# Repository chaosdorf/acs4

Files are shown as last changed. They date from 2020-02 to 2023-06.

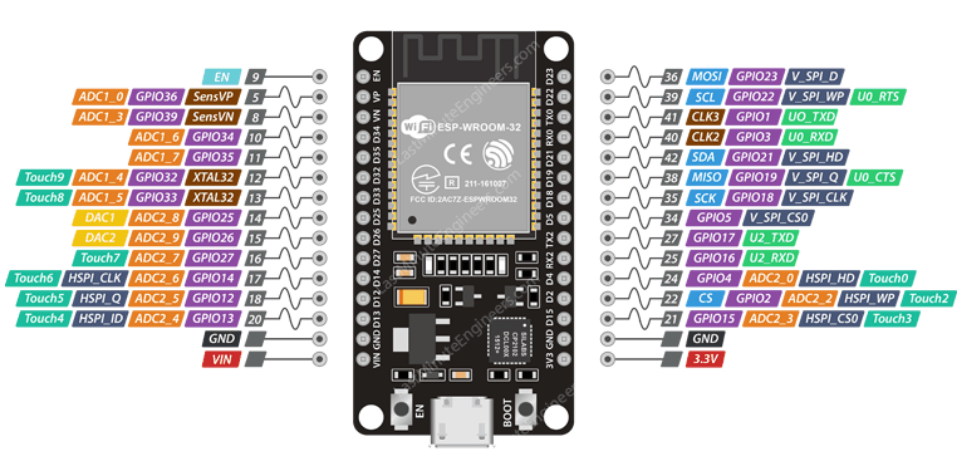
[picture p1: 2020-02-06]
pcb/prototyp/slave/ESP32_Pinout.png

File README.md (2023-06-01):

# Access control system 4 

Die (geplante) Türsteuerung für die Türen im neuen Dorf auf der Sonnenstraße.

## Benutzung

Gäste können die Klingel betätigen, dann klingelt es.

Mitglieder können mit ihrem iButton oder SSH-Key die Tür temporär öffnen.

(public schalten wie im alten Dorf ist in diesem Haus wohl leider unpraktikabel.)

Einzelne Menschen sind in der Lage, Schlüssel zu registrieren und zu revoken.

## Hardware

Fürs Erste haben wir eine Minimallösung vor mit nur einer Platine mit einem ESP32-C3:

- speichert die iButton-IDs
- steuert die Aktoren an 12V Output
- Unlock über WiFi (SSH-Emulation)
- Update der IDs über Git
- gute Rust-Unterstützung

<details>
<summary>Die vollständige Lösung sollte auf zwei Platinen aufgeteilt sein:</summary>

[Blockschaltbild](src/Blockbild_Uebersicht_rev04.pdf)

### Server-Board
- Steuert die Aktoren an 12V Output
- Speichert die iButton IDs auf einer SD
- Ethernet nutzt ein Olimex Board ESP32 rev E
- Stromausfall erkennung

[Olimex Shop](https://www.olimex.com/Products/IoT/ESP32/ESP32-GATEWAY/open-source-hardware)

[Github Projekt Olimex](https://github.com/OLIMEX/ESP32-GATEWAY/tree/master/HARDWARE)

[ESP32 Gateway Schematic rev E](src/ESP32-GATEWAY_Rev_E_color.pdf)

### Client-Board
- iButton Reader
- LED Output
- Klingel Taster input 1
- Klingel Taster input 2
- Display output für eInk
- WS2812 LED Output

(jeweils für Außen- und Innentür)

[Waveshare eInk - Shop](https://eckstein-shop.de/Waveshare-27-inch-264x176-E-Ink-E-Paper-Raw-Display-three-color-Arduino)

</detail>

### Elektrisches Schloss
Unsere Tür hat drei Modi:
 * zu (Panikfunktion)
 * Summer
 * offen

Wir hatten überlegt, einen Motor an den Schlosszylinder anzuschließen, um zwischen diesen drei Modi umschalten zu können.
(Bei unserem Versuch mit einem Abus-Motor stand dann allerdings die Tür offen, weil sich der Motor unbedingt neu kalibrieren musste.)

Deswegen ist es wohl am einfachsten, die Tür einfach in dem Summer-Zustand zu lassen.

## Software

### Schlüsselspeicherung

Die Schlüssel liegen als Dateien in einem Git-Repo vor:

Es gibt beliebig viele `username-description.key`-Dateien,
die jeweils eine Zeile mit einer iButton-ID bzw. einem SSH-Key enthalten, z.B.:

```
ssh-ed22519 AAAAAAAAAAAAAAAAAAAAAAAAAAAAAAAA
```

```
iButton 1234567890
```

Sie ist ist signiert (minisign) von der ausstellenden Person und verschlüsselt (age) mit
 * einem gemeinsamen Public-Key
 * allen Public-Keys der Menschen aus dem Schlüssel-Team (diese sind auch im Repo hinterlegt)

Irgendwo läuft eine Software, die sich diese Änderungen zieht,
die die Dateien entschlüsselt und verifiziert und dann einen großen Blob erzeugt
und den verschlüsselt (mit libhydrogen).
Der ESP zieht sich davon regelmäßig die neueste Version.

Bis diese Software existiert, wird die große Schlüsselliste manuell geführt.

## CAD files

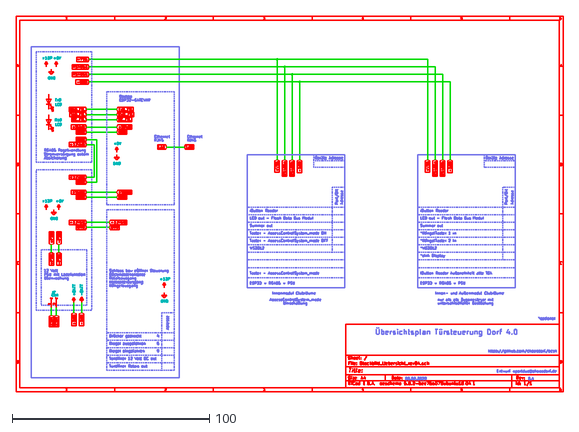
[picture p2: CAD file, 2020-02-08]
src/blockschaltbild/images/Blockbild_Uebersicht_rev04.dxf
277.0 x 190.0

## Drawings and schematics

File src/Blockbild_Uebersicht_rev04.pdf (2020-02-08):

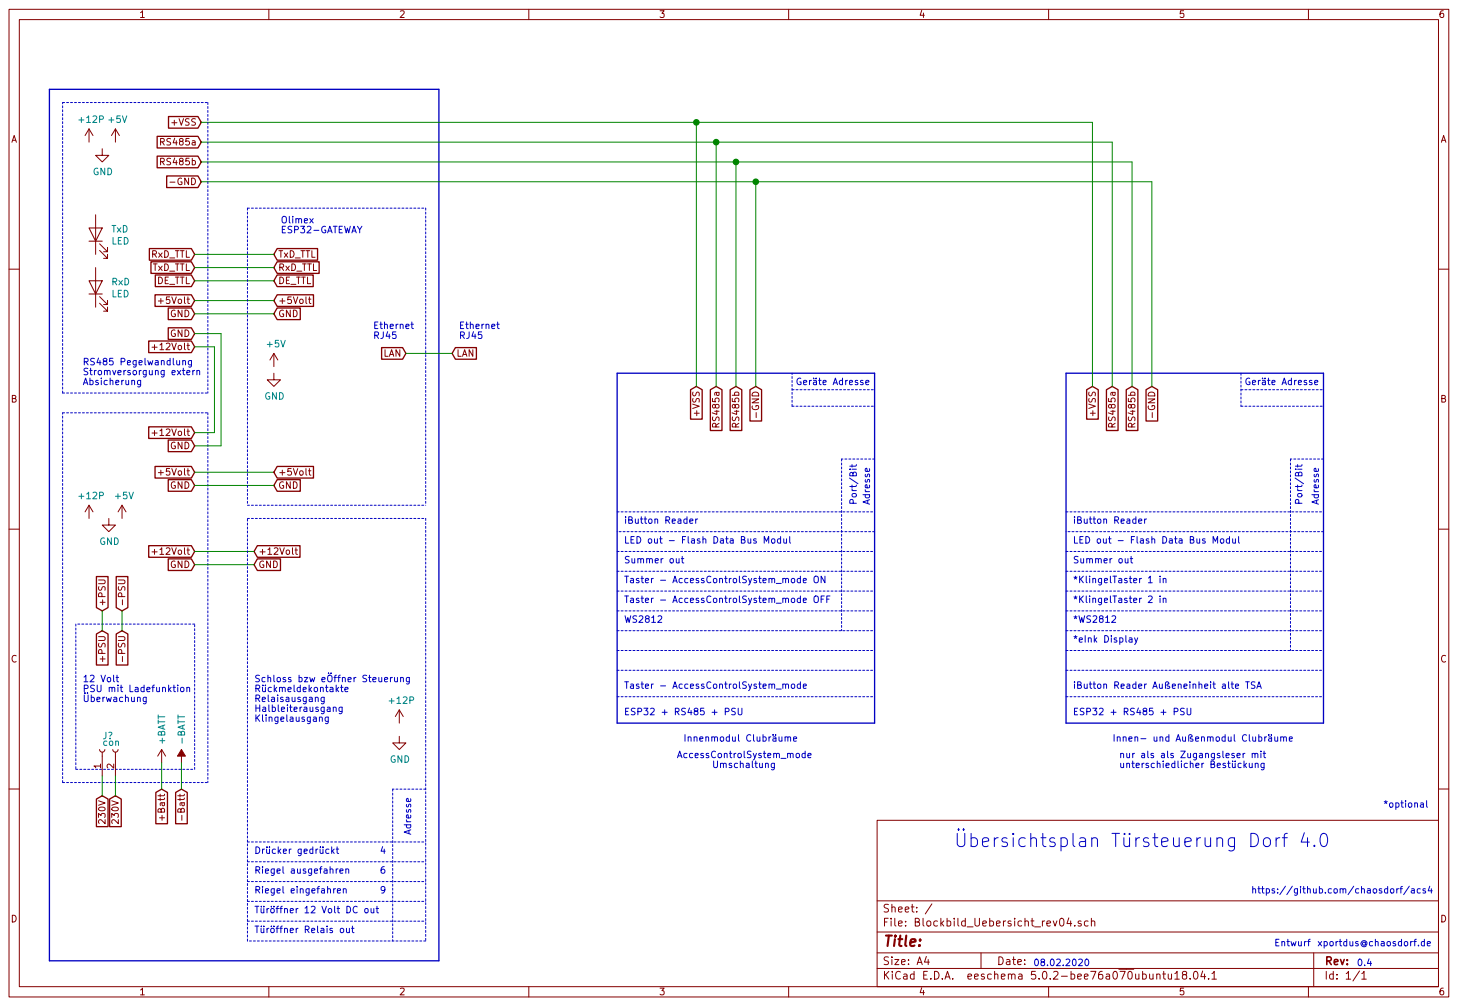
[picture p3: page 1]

iButton Reader *KlingelTaster 2 in

LED out - Flash Data Bus Modul Taster - AccessControlSystem_mode OFF

Taster - AccessControlSystem_mode ON WS2812

Schloss bzw eÖffner Steuerung Rückmeldekontakte Relaisausgang

iButton Reader Außeneinheit alte TSA

Innen- und Außenmodul Clubräume nur als als Zugangsleser mit

Türöffner Relais out Türöffner 12 Volt DC out Riegel ausgefahren Riegel eingefahren

Entwurf https://github.com/chaosdorf/acs4

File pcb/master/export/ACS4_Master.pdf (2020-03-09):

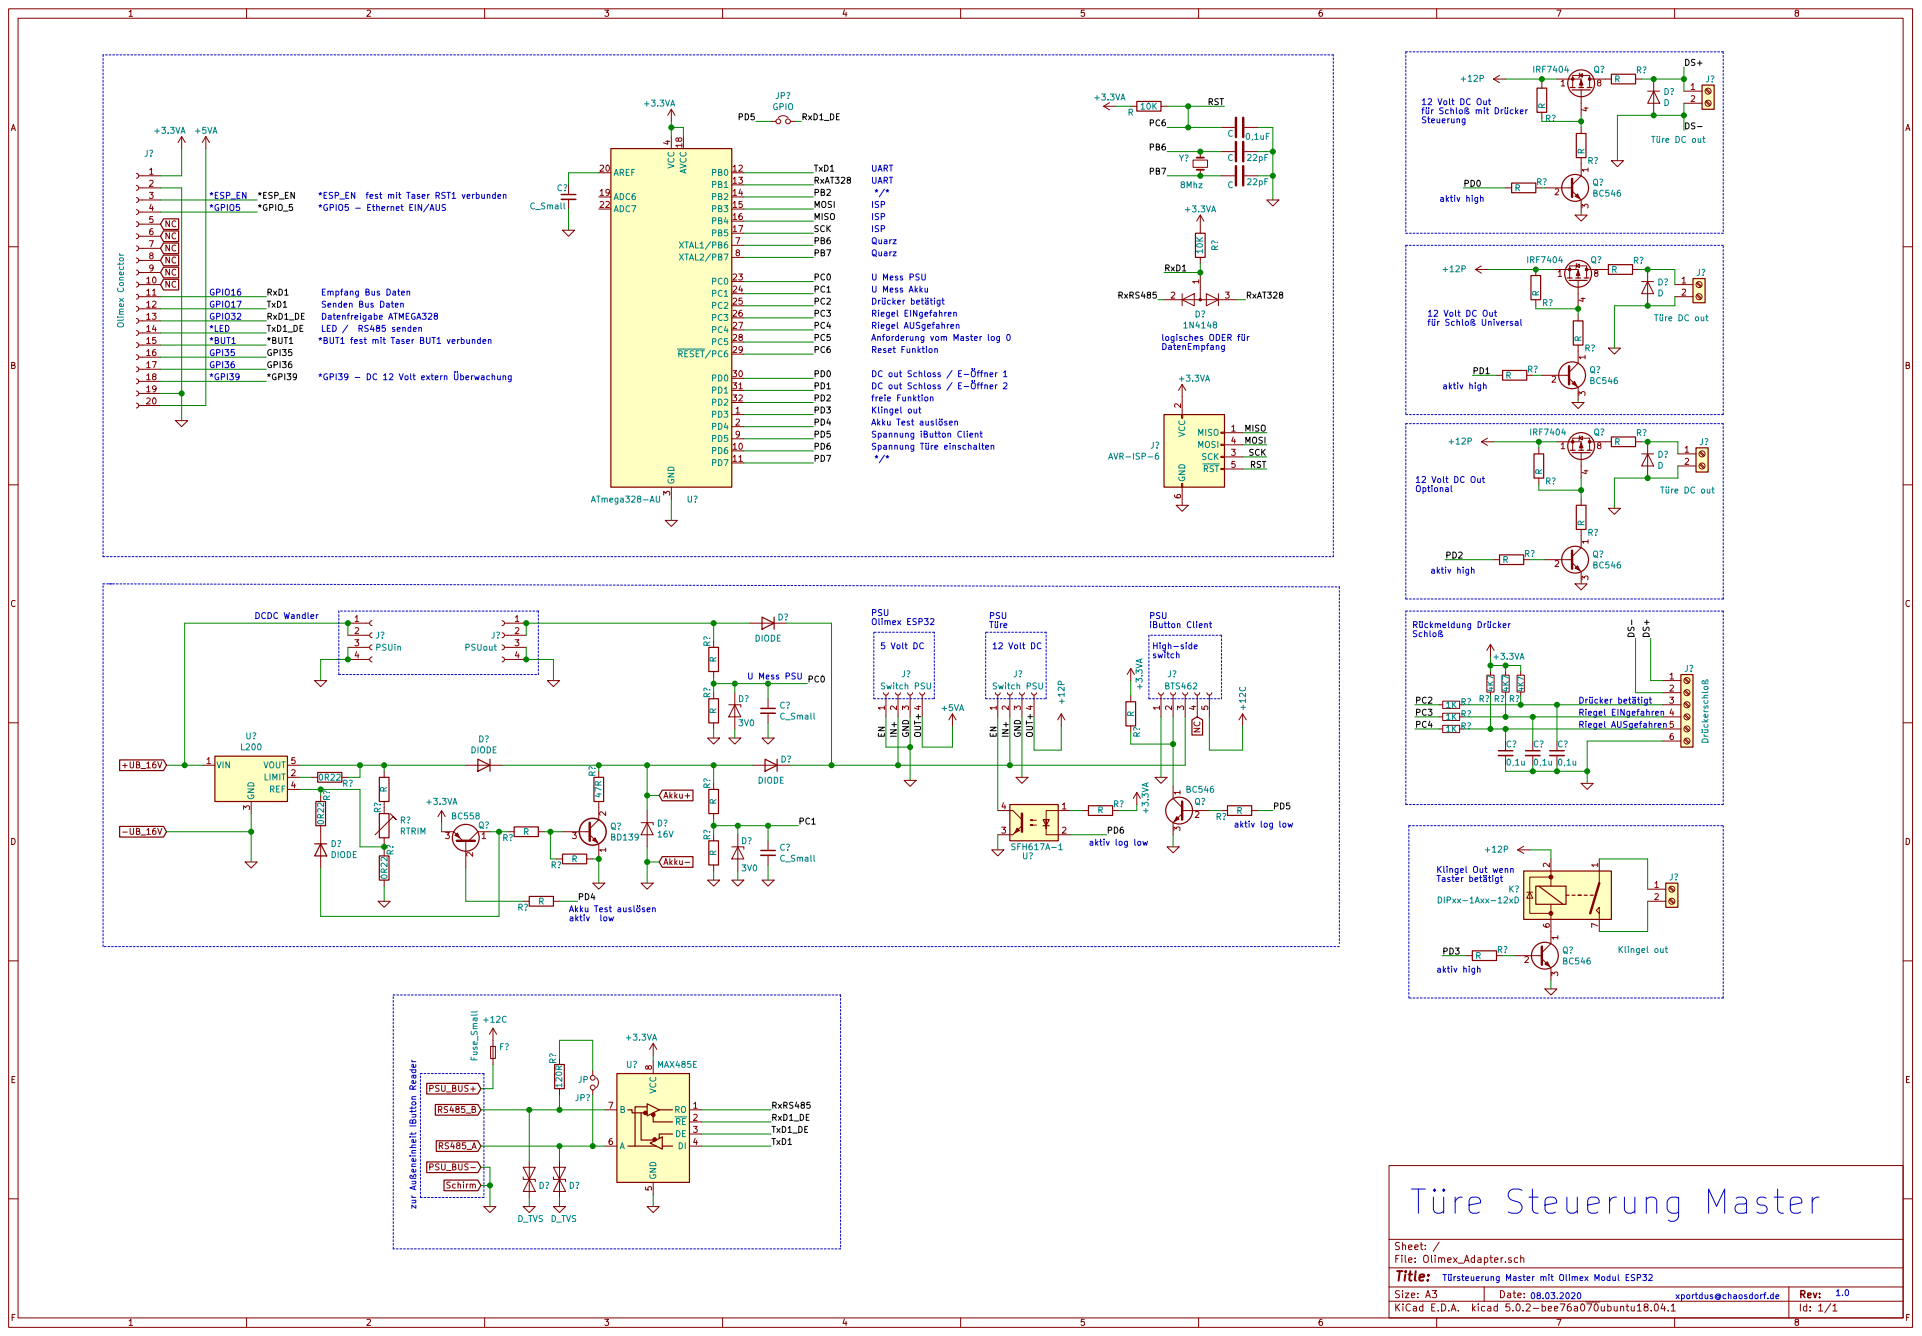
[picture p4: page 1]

U Mess PSU Quarz Quarz Spannung Türe einschalten Reset Funktion Drücker betätigt

12 Volt DC Out
für Schloß mit Drücker Steuerung

Riegel EINgefahren
Riegel AUSgefahren
Anforderung vom Master log 0

für Schloß Universal 12 Volt DC Out Optional R? R

DC out Schloss / E-Öffner 1
DC out Schloss / E-Öffner 2

*GPI39 - DC 12 Volt extern Überwachung

2 SCK 3 MOSI 4 RST 5 GND

Riegel EINgefahren 4

Akku Test auslösen aktiv low

File: Olimex_Adapter.sch Sheet: / Türe Steuerung Master

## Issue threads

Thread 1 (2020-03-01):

Schlüsselliste auf das Gerät bekommen

YtvwlD, 2020-03-01:
## allgemeine Beschreibung

Wir wollen ja iButtons nutzen, um die Türen zu öffnen. Dazu muss auf allen Geräten eine Liste vorhanden sein, welche iButtons berechtigt sind, die Türen zu öffnen. Dabei gibt es grob vier Anforderungen:

 * Schlüssel müssen zentral hinzugefügt werden können (z.B. Ausgabe an Neumitglieder)
 * Schlüssel müssen zentral entfernt werden können (z.B. Verlust eines Schlüssels)
 * die Liste von Schlüsseln darf nicht von Unbefugten gelesen werden (sowohl bei der Übertragung, als auf dem Speicher des Geräts); ansonsten können Schlüssel geklont werden
 * die Liste von Schlüsseln darf nicht von Unbefugten verändert werden (sowohl bei der Übertragung, als auf dem Speicher des Geräts); ansonsten können Schlüssel hinzugefügt werden

Das sind also zwei Ebenen: die Verteilung und die Integrität / Vertraulichkeit.

## Ansätze für Verteilung

### HTTPS

 * kann mit Client-Zertifikaten oder Auth-Headern auch direkt Integrität und Vertraulichkeit sicherstellen
 * Polling nötig
 * eigener Server nötig

###  mqtt

 * PubSub
 * bietet Transportverschlüsselung, aber keine Berechtigungen (?)
 * Infrastruktur vorhanden

## Ansätze für Integrität / Vertraulichkeit

### PGP

 * antik
 * komplex
 * läuft das überhaupt auf Microcontrollern?
 * kann sowohl asymmetrische als auch symmetrische Crypto

### minisign + age

 * modern
 * simpel
 * läuft leider nicht ohne Schmerzen auf Microcontrollern
 * kann asymmetrische Crypto (geht auch symmetrische?)

### libhydrogen

 * modern
 * simpel
 * wie gemacht für Microcontroller
 * kann nur symmetrische Crypto

## Fazit

Ich habe das kurz mit @A2nkF diskutiert, unser Vorschlag für das Prozedere zum Hinzufügen bzw. Entfernen von Schlüsseln:

 1. neue Liste auf einem Server (Docker-Container?) mit https://github.com/jedisct1/libhydrogen/wiki/Secret-key-encryption und einem Pre-Shared Key verschlüsseln
 2. das über MQTT jagen
 3. auf den Geräten dies verifizieren und decrypten
 4. die gecryptete Version auf die SD-Karte speichern
 5. beim jedem Start die Datei decrypten und verifizieren

### Vorteile

 * einfach zu implementieren auf Microcontrollern (+ nette API)
 * Daten verschlüsselt auf den Geräten (-> SD-Karte rausziehen bringt quasi nichts)
 * Daten werden selten übertragen (nur bei Änderungen) (-> schwieriger abzufangen)

### zu beachten

PSK-Verlust bedeutet Verlust der Schlüsselliste, aber:
PSK kann nur erlangt werden durch Zugriff auf eins der beteiligten Geräte (oder den Server), aber diese Geräte haben auch die Schlüsselliste, von daher egal.

nomaster, 2020-03-06:
Ich empfehle, das Ausrollen neuer Schlüssel direkt von einem gesicherten Arbeitsgerät aus zu tun. Ein Service auf einer geteilten Hardware ist m.E. nicht sicher zu betreiben.

YtvwlD, 2020-03-06:
Wir haben das gerade eben nochmal gesprochen und sind der Ansicht, dass ein zentrales Gerät gangbar ist. Wir müssen die Schlüssel irgendwie verwalten und "jede\*r macht das auf dem eigenen Gerät" ist halt mit eigener Hardware auch nicht geil - und schwierig zu synchronisieren.
Auch: So wahrscheinlich ist ein erfolgreicher Angriff jetzt auch nicht. So eine Standard-Django/Rails-Anwendung ist schon relativ stabil und sicher.

YtvwlD, 2020-03-07:
Wobei durch die Auslieferung per unregelmäßiger, verschlüsselter mqtt-Nachrichten das System, dass die Primärliste hält ja gar nicht dauerhaft online sein muss.
Das heißt, wir können dafür tatsächlich einfach einen Pi oder Ähnliches nehmen, da LUKS draufpacken und den im schlimmsten Fall sogar wegschließen. Wir brauchen das Gerät ja nur für Änderungen.

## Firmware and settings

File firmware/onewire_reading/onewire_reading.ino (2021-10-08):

#include <OneWire.h>
 
OneWire ibutton (2); // iButton connected on PIN 42.
 
byte buffer[8];
 
void setup(){
  Serial.begin(115200);
  Serial.println("Hello"); // print new line
}
 
void loop(){
  // Search for an iButton and assign the value to the buffer if found.
  if (!ibutton.search (buffer)){
     ibutton.reset_search();
     delay(250);
     return;
  }
  // At this point an iButton is found
  Serial.println("1-Wire Device Detected, ID is:");
 
  for (int x = 0; x<8; x++){
    Serial.print(buffer[x],HEX);
    Serial.print(" ");
  }
  Serial.print("\n");
 
  // Check if this is a iButton
  if ( buffer[0] != 0x01) {
    Serial.println("Device is not an iButton");
  } else {
    Serial.println("Device is an iButton");
  }
 
  if ( ibutton.crc8( buffer, 7) != buffer[7]) {
      Serial.println("CRC is not valid!");
  }
  Serial.println("Done.\n\n");  
}

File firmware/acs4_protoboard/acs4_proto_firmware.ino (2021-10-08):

#include <OneWire.h>
#include "FS.h"
#include "SPIFFS.h"
#define FORMAT_SPIFFS_IF_FAILED false
 
OneWire iButton (25); // iButton connected on PIN 25.

int summer = 4;
int relais = 5;
int led = 32;


#define OK              0   //correct key read
#define NO_ADDR         1   //No address found
#define CRC_invalid     2   //invalid CRC
#define NOT_DS1990      3   //invalid family code (0x01=DS1990A, 0x81=custom iButton, these are valid)
 
byte buffer[8];

int ledState = LOW;
unsigned long previousMillis = 0; 
 
void setup(){
  Serial.begin(115200);
  Serial.println("Hello"); // print new line

  pinMode(summer, OUTPUT);
  pinMode(relais, OUTPUT);
  pinMode(led, OUTPUT);

  digitalWrite(summer, LOW);   
  digitalWrite(relais, LOW);   
  digitalWrite(led, LOW);   

    if (!SPIFFS.begin(FORMAT_SPIFFS_IF_FAILED)) {
    Serial.println("SPIFFS Mount Failed");
    return;
  }
}

byte nibble(char c)
{
  if (c >= '0' && c <= '9')
    return c - '0';

  if (c >= 'a' && c <= 'f')
    return c - 'a' + 10;

  if (c >= 'A' && c <= 'F')
    return c - 'A' + 10;

  return 0;  // Not a valid hexadecimal character
}


void hexCharacterStringToBytes(byte *byteArray, const char *hexString, byte startAt = 0)
{
  bool oddLength = strlen(hexString) & 1;

  byte currentByte = 0;
  byte byteIndex = 0;

  for (byte charIndex = startAt; charIndex < strlen(hexString); charIndex++)
  {
    bool oddCharIndex = charIndex & 1;

    if (oddLength)
    {
      // If the length is odd
      if (oddCharIndex)
      {
        // odd characters go in high nibble
        currentByte = nibble(hexString[charIndex]) << 4;
      }
      else
      {
        // Even characters go into low nibble
        currentByte |= nibble(hexString[charIndex]);
        byteArray[byteIndex++] = currentByte;
        currentByte = 0;
      }
    }
    else
    {
      // If the length is even
      if (!oddCharIndex)
      {
        // Odd characters go into the high nibble
        currentByte = nibble(hexString[charIndex]) << 4;
      }
      else
      {
        // Odd characters go into low nibble
        currentByte |= nibble(hexString[charIndex]);
        byteArray[byteIndex++] = currentByte;
        currentByte = 0;
      }
    }
  }
}


void dumpByteArray(const byte * byteArray, const byte arraySize)
{

for (int i = 0; i < arraySize; i++)
{
  Serial.print("0x");
  if (byteArray[i] < 0x10)
    Serial.print("0");
  Serial.print(byteArray[i], HEX);
  Serial.print(", ");
}
Serial.println();
}


/*
 * Checks if a raw key code (from the reader) exists in the key file and reads that data into
 * the global key var. If the key is not present in our file the key status will be set to KEY_UNKNOWN
 * if an error occurred during reading the key status will be set to CANNOT_COMPARE
 */
bool CheckKey(byte *rawkey){

File root = SPIFFS.open("/");
File file = root.openNextFile();
while (file) {
  if (!file.isDirectory()) {
    if (strlen(file.name()) != 17)
    {
      break;
    }
 
    byte fileKey[8] = {0};   
    hexCharacterStringToBytes(fileKey,file.name(),1);
    //dumpByteArray(rawkey, 8);
  
    if (memcmp(rawkey, fileKey, 8) == 0)
    {
      Serial.print(" Key found!");
      return true;
    }
     
  }  
  file = root.openNextFile();
}
Serial.print(" Key not found!");
return false;



//  File dataFile = SD.open(keyfile, O_READ);
//  if (!dataFile){
//    fileerror(keyfile);
//    memcpy(key.keycode,rawkey,8);       //remember key
//    key.keystatus=CANNOT_COMPARE;
//    key.keyname[0]=0;
//    return;
//  }
//  while (readkey(dataFile)){
//    if (!memcmp(rawkey,key.keycode,8)){     //key found in keyfile
//      dataFile.close();
//      return;
//    }
//  }
//  dataFile.close();
//  //key not in keyfile
//  memcpy(key.keycode,rawkey,8);         //remember key
//  key.keystatus=KEY_UNKNOWN;
//  key.keyno=0;
//  strcpy(key.keyname,"unknown key");
}


byte getKeyCode(byte* rawkey){
  if ( !iButton.search(rawkey)) {
    iButton.reset_search();
    return NO_ADDR;
  }
  if ( OneWire::crc8( rawkey, 7) != rawkey[7]) {
    return CRC_invalid;
  }
  if ( (rawkey[0] & 0x7F) != 0x01 && rawkey[0] != 0x08) { //0x01=DS1990A (if MSB=1 custom made iButton (0x81)) or 0x08=DS1992 with 1024bits of NV memory
    return NOT_DS1990;
  }
 
  iButton.reset();

  for (byte i=0; i<4;i++)
  {
    byte mem = rawkey[i];    
    rawkey[i]=rawkey[7-i];
    rawkey[7-i]=mem;  
  }

  Serial.print("\nKey gelsen:"); 
  for (byte i = 0;i<8;i++){
    if (rawkey[i] < 16)
    {
      Serial.print(0,HEX); 
    }
    Serial.print(rawkey[i],HEX); 
  }
  
  return OK;
}
 



void loop(){
  unsigned long currentMillis = millis();
  byte rawkey[8];  
  byte readresult;

  digitalWrite(led, HIGH); 

  readresult = getKeyCode(rawkey);
  if (readresult == OK) {
    if (CheckKey(rawkey))
    {
      //opendoor
      Serial.print(" Access granted");  
      
      digitalWrite(summer, HIGH);   
      digitalWrite(relais, HIGH);   
      digitalWrite(led, LOW);
           
      delay(3000); 
      
       
      digitalWrite(summer, LOW);   
      digitalWrite(relais, LOW);   

      delay(5000); 

      digitalWrite(summer, HIGH);   
      digitalWrite(relais, HIGH);

      delay(3000); 
      
      digitalWrite(summer, LOW);   
      digitalWrite(relais, LOW);
      digitalWrite(led, HIGH);  
    }
    else
    {
      digitalWrite(led, LOW); 
      delay(15000); //If wrong Key / bruteforce attack -> wait 15sec
      digitalWrite(led, HIGH);
    }
  }  
  
}

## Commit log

2020-02-06 Tabelle in der Reame upgedated
2020-02-06 Update Readme und Schaltplan ESP32 Ethernet Board
2020-02-08 Blockschaltbild verschoben und die Projektdatei hinzugefügt
    [Blocbild_Ubersicht.sch.sch, Blocbild_Ubersicht_rev02.sch, Blocbild_Ubersicht_rev03.sch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]
2020-03-09 Update vom Master
    [ACS4_Master.sch]
2020-10-28 Status zum Motorschloss aktualiersiert
2020-10-31 fix grammar
    if the first character of the referenced word is a vowel, use `an` instead of `a`
    [onewire_reading.ino]
2021-10-08 Quellcode des Controllers der aktuell die Türe im Dorf öffnet hinzugefügt
2023-06-01 Minimallösung mit nur einem Board
